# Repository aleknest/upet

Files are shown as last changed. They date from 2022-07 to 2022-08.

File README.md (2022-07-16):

# upet

[Відео роботи верстата](https://youtu.be/OY4By4eS6UQ)

[Список комплектуючих верстата](./bom/bom_machine.txt).

[Список комплектуючих підтримувача бобіни з лентою](./bom/bom_spool.txt).

[Список комплектуючих підтримувача бобіни з філаментом для принтера](./bom/bom_printer.txt).

Бобіни для порізаної ленти: https://www.thingiverse.com/thing:1848206

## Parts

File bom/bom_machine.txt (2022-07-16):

    100K NTC 3950 Thermistor
    4020 slot: 145mm
    685 bearing
    DIN 6798A washer
    Heater Cartridge 12V 40W 6*20mm
    Led power supply MN-100W12V, size 175*53*21mm, https://www.aliexpress.com/item/1005002290063769.html
    M3 nut (hex), 7 pcs
    M3 nut (thin square), 6 pcs
    M3 t-slot nut, 2 pcs
    M3 washer, 15 pcs
    M3x10 DIN912, 11 pcs
    M3x30 DIN912, 2 pcs
    M3x35 DIN912, 4 pcs
    M3x6 DIN912, 2 pcs
    M4 washer, 2 pcs
    M5 nut, 8 pcs
    M5 t-slot nut, 4 pcs
    M5 washer, 13 pcs
    M5x10 DIN912, 8 pcs
    M5x16 bolt, 2 pcs
    M5x16 DIN912
    M5x20 DIN912, 6 pcs
    M5x30 bolt
    M6x10 or M6x12 bolt
    Nema 17 motor
    optical switch
    Volcano heatblock

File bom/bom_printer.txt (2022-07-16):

    M5 nut, 8 pcs
    M5 t-slot nut, 2 pcs
    M5 washer, 8 pcs
    M5x10 DIN912, 2 pcs
    M5x16 bolt, 2 pcs
    M5x20 DIN912, 6 pcs

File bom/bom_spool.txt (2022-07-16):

    608 bearing
    M3 nut (hex), 2 pcs
    M3 washer, 2 pcs
    M3x20 DIN912, 2 pcs

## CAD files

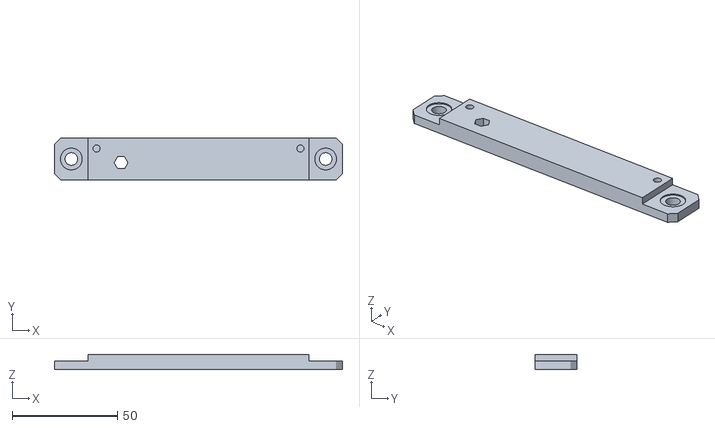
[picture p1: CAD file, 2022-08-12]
produce/board/plate.stl
137.0 x 20.0 x 6.99

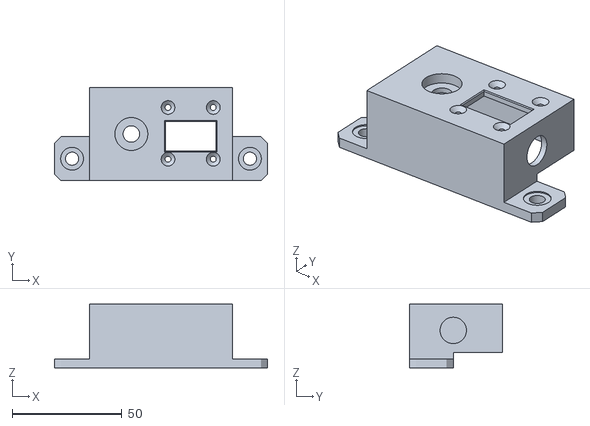
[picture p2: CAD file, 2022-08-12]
produce/display/box.stl
97.0 x 42.5 x 29.1

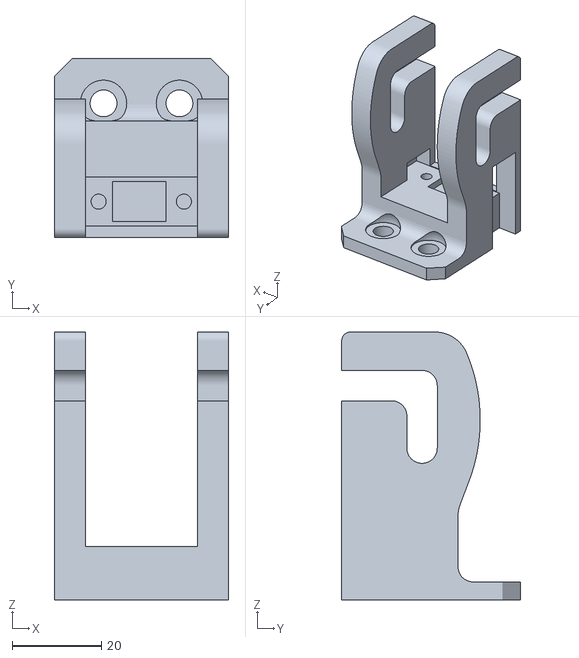
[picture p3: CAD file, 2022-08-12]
produce/main/endstop.stl
39.0 x 40.0 x 60.0

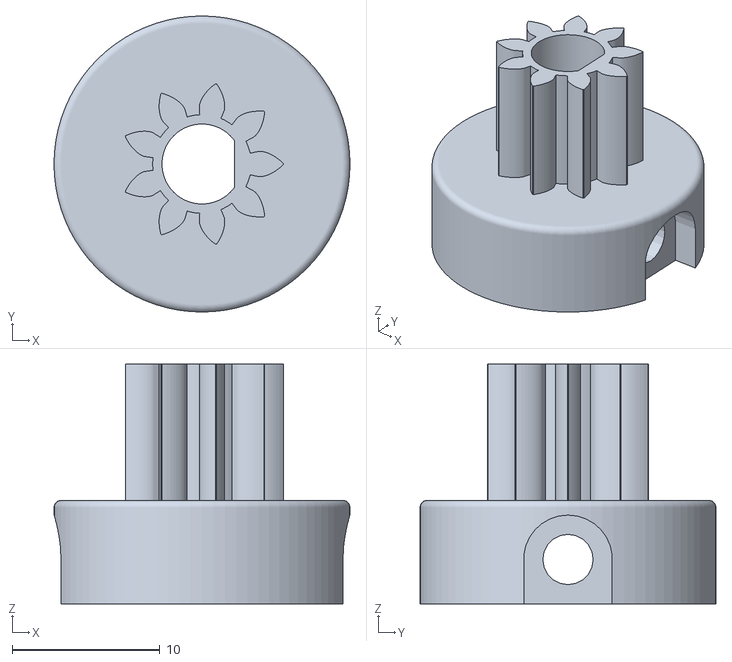
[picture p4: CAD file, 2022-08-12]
produce/planetary/planetary_sun.stl
20.0 x 20.0 x 16.2

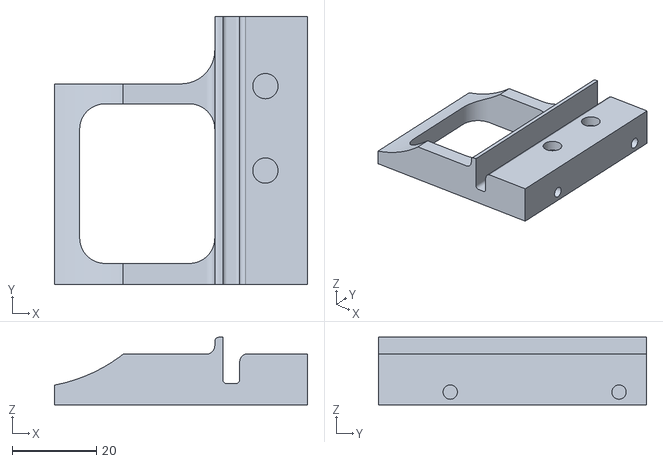
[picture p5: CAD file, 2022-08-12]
produce/power_supply/fix_left.stl
60.0 x 63.5 x 16.0

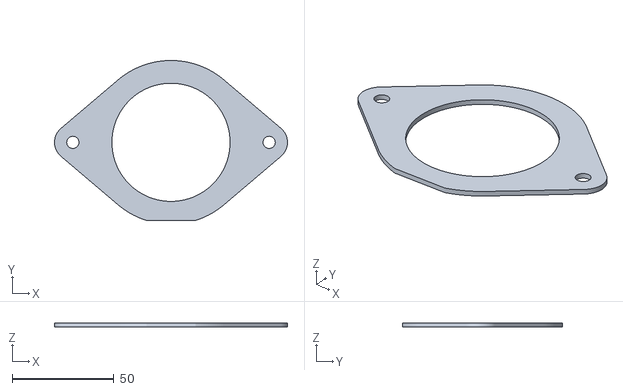
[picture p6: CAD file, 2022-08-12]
produce/printer/filament_case_top.stl
114.4 x 78.6 x 2.00

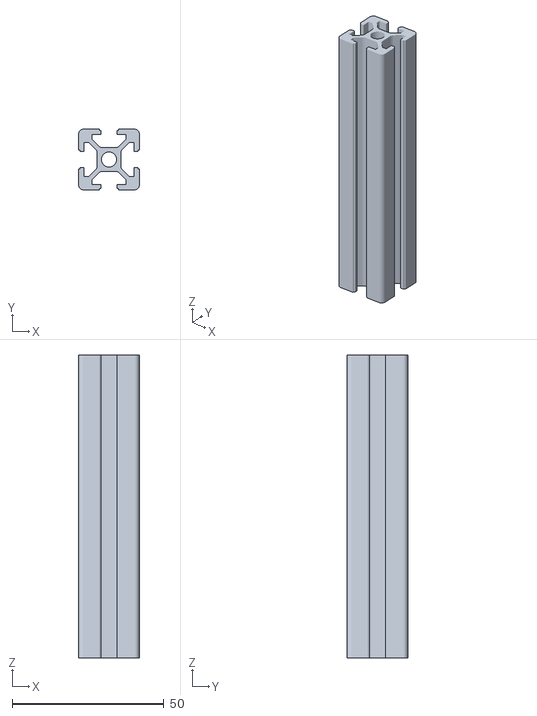
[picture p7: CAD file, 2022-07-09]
proto/slot2020.stl
20.0 x 20.0 x 100.0

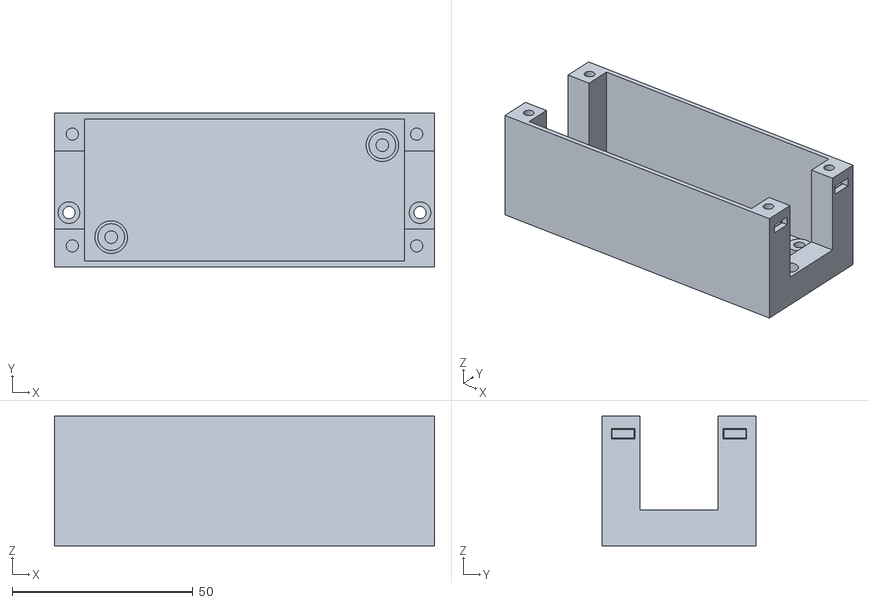
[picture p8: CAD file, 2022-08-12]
produce/board/bottom.stl
105.0 x 42.5 x 35.9

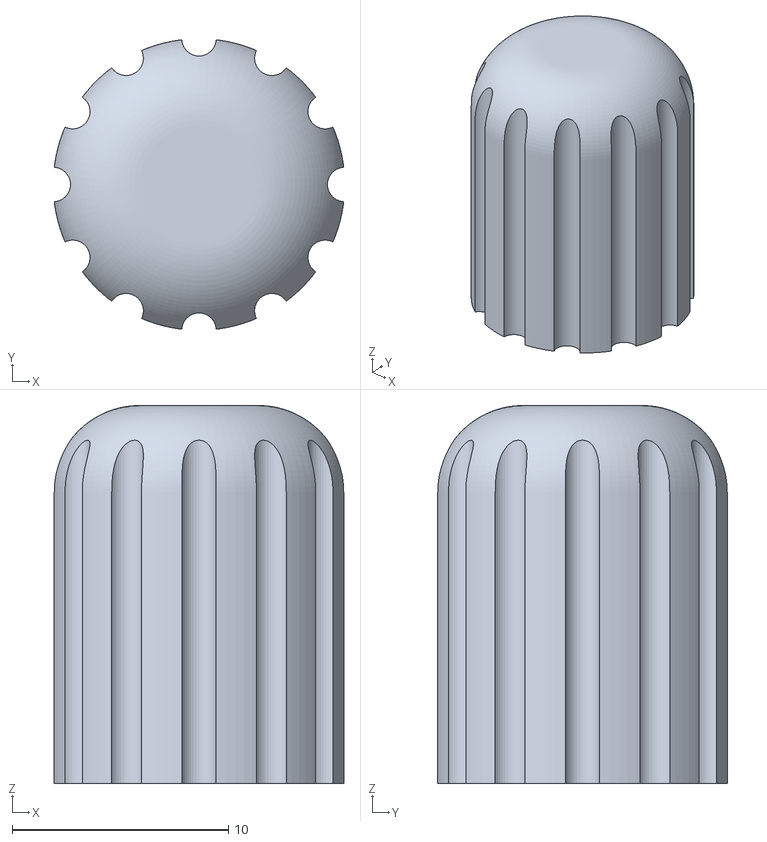
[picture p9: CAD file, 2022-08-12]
produce/display/encoder_knob.stl
13.4 x 13.4 x 17.5

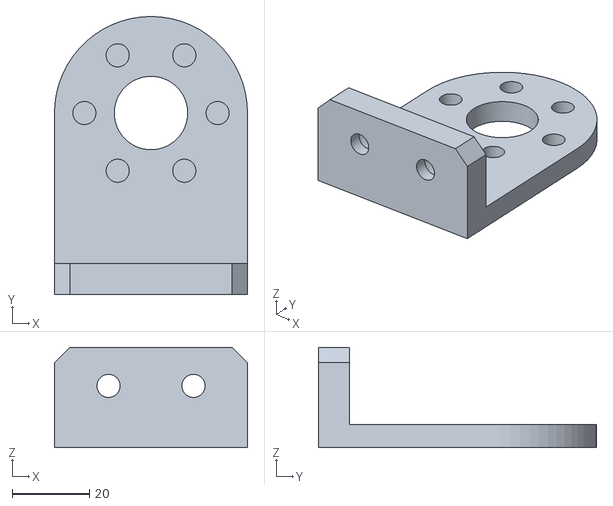
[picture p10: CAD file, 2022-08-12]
produce/main/stand.stl
50.0 x 72.0 x 26.0

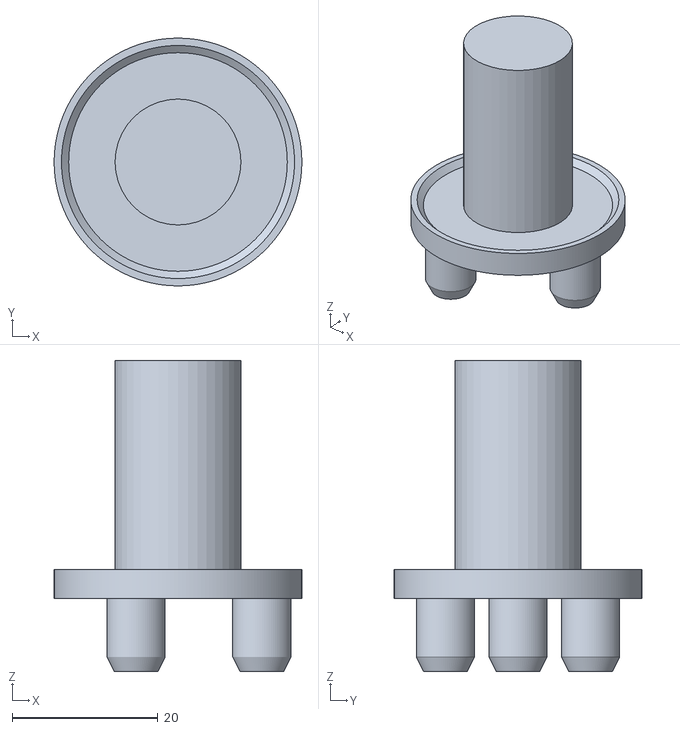
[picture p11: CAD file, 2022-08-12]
produce/planetary/planetary_carrier.stl
34.0 x 34.0 x 42.7

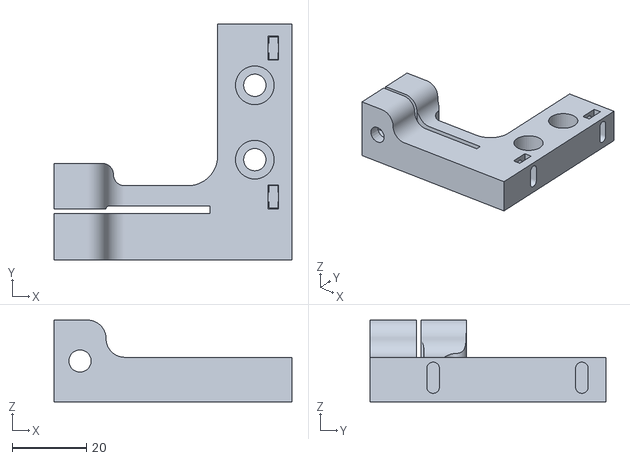
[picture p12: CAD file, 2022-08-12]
produce/power_supply/fix_right.stl
64.0 x 63.5 x 22.0

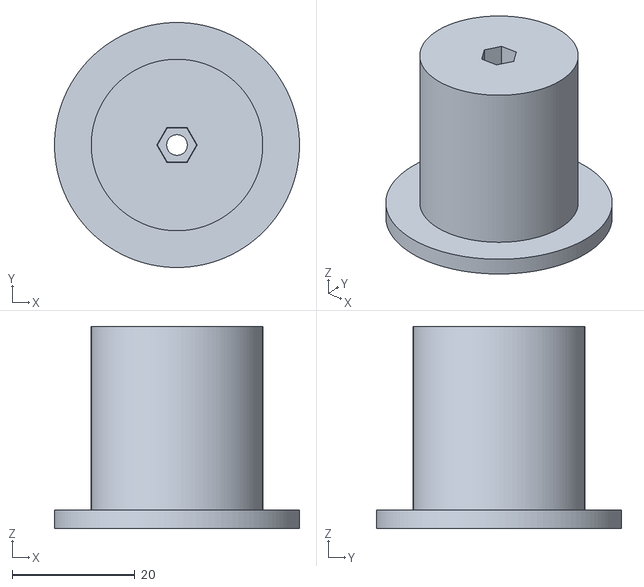
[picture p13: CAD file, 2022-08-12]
produce/spool/top.stl
40.0 x 40.0 x 33.0

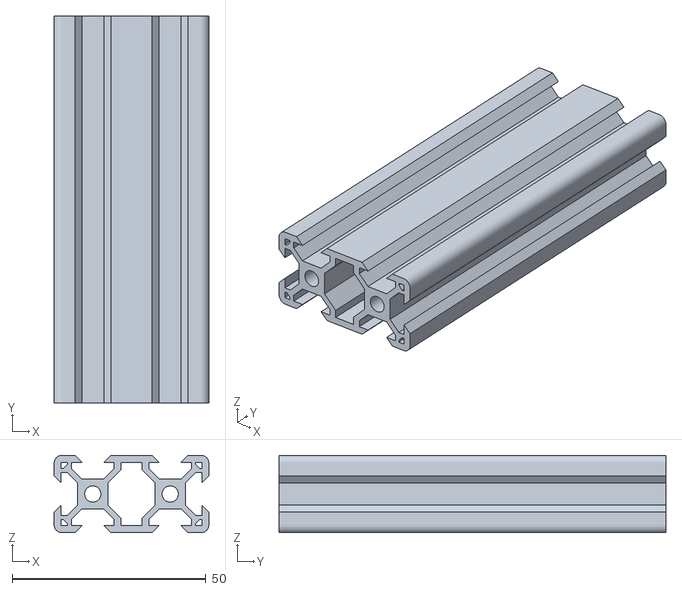
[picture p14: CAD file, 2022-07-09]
proto/40x20x100VSlotExtrusion.stl
40.0 x 100.0 x 20.0

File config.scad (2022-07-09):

include <../_utils_v2/NopSCADlib/core.scad>
include <../_utils_v2/NopSCADlib/vitamins/stepper_motors.scad>
include <../_utils_v2/NopSCADlib/vitamins/extrusion_brackets.scad>

use <../_utils_v2/Getriebe.scad>
use <../_utils_v2/_round/polyround.scad>
use <../_utils_v2/fillet.scad>
use <../_utils_v2/m3-m8.scad>

slot=40;

//                          corner  body    boss    boss          shaft
//                          side, length, radius, radius, radius, depth, shaft, length,      holes, cap heights
NEMA17ali  = ["NEMA17ali",   42.3, 38.3,     53.6/2, 25,     11,     2,     5,     24,          31,    [11.5,  9]];

eingriffswinkel=10;
gear_big_steigungswinkel=10;
gear_big_modul=1;
gear_big_d=70;
gear_small_d=3;
gear_big_h=8-2;
gear_small_h=30;
small_gear_r = gear_small_d/(2*sin(gear_big_steigungswinkel));

filament_fix_screw=18+2;	

// inner diameter, outer diameter, height, cap diameter,cap thickness
body_dim = [33-13,60-18,40,gear_big_d,3];
big_gear_tr=[[0,0,gear_big_d/2],[0,90,-90]];
big_gear_mirror=false;
small_gear_mirror=true;
small_gear_block_mirror=false;
small_gear_angle=180;//75+60;
small_gear_tr=[[0,0,-small_gear_r],[0,0,90]];
small_gear_fix_tr=[[gear_small_h/2+4,0,-small_gear_r],[0,0,90]];
motor_tr=[vec_add(small_gear_tr[0],[-40,0,0]),[0,90,0]];
small_gear_pad_tr=[vec_add(motor_tr[0],[4,0,0]),motor_tr[1]];

small_gear_pad=[small_gear_r*2,abs(motor_tr[0].z-small_gear_tr[0].z)
	+abs(motor_tr[0].x-small_gear_tr[0].x)-16.8];
// inner diameter, height, cap diameter,cap thickness
spool_axis=[body_dim[0]-1,body_dim[2],body_dim[0]+30,14];
spool_axis_tr=[[0,0,gear_big_d/2],[90,0,0]];

stand_zadd=4;
stand_slot_th=8;
//width,height,thickness,spool fix diameter and thickness
stand = [50,gear_big_d/2,6,spool_axis[2],6];
stand_tr=[[0,spool_axis[3],0],[90,0,180]];

// outer,height,inner
bearings = [
 [10,4,5] //mr105zz
,[11,5,5] //685zz
,[16,5,5] //625zz
,[10,4,3] //623zz
,[9,3,5] //mr95
,[16,5,8] //688zz
,[22,7,8] //608zz
];
small_gear_bearing=bearings[1];
//thickness,bottom
small_gear_bearing_p=3;
nobearing=false;

slot_length=145;
slot_tr=[slot_length/2-30,-slot+20,-stand_slot_th-stand_zadd-10];
volcano_tr=[slot_length-55,-12,-3.5];
brdiff=14.2;
bradd=1+0.3;
bracket_tr_y=volcano_tr.y+26;
bracket_tr_z=volcano_tr.z-8.5;
bracket_outer=[4,3];
bracket_tr=[
	  [[volcano_tr.x-brdiff+bradd,bracket_tr_y,bracket_tr_z],[0,0,-90]]
	 ,[[volcano_tr.x+brdiff+bradd,bracket_tr_y,bracket_tr_z],[0,0,-90]]
];


power_to_slot_out=7.5+3;
power_to_slot_left_dim=[24/2,53+power_to_slot_out,20+40];
power_to_slot_right_fix=14;
power_to_slot_right_x=10;
power_to_slot_right_dim=[24/2+power_to_slot_right_x,53+power_to_slot_out,50+power_to_slot_right_fix];
slot_left_tr=[[slot_tr.x-slot_length/2,slot_tr.y-power_to_slot_out/2+14,slot_tr.z-10],[0,0,0]];
slot_right_tr=[[slot_tr.x+slot_length/2,slot_tr.y-power_to_slot_out/2+14,slot_tr.z-10],[0,0,180]];
power_to_slot_up=[2,4];
power_to_slot_cut=[4,7];

endstop_thickness=3;
endstop_top=34+14+4;
endstop_dim=[31,26,4];
endstop_tr=[-12-60,-8-22-24,-4];

endstop_screw_d=6;
endstop_screw_out=2;
endstop_screw_tr=[10,22];

endstop_tube=14;

endstop_up=8;
endstop_back=40-20;

motor_out=2;

//thickness bottom
filament_case=[2,2+1.6+1.6];

spool_bearing=bearings[6];
// bottom part(bottom,top),bottom height; top part height,thickness,diameter
//,fix height diameter
spool_dim=[90,40,10+5,2,3,40,30,28];

oled_width=27.3;
oled_height=27.75;
screen_width=23;
screen_height=13.5;
function stand_tr(x,y)=[(oled_width/2-2.1-2.5/2)*x,(oled_height/2-2.1)*y-0.3,0];

function vec_add (v1,v2)=[v1.x+v2.x,v1.y+v2.y,v1.z+v2.z];
module translate_rotate(tr) 
{
	for (i=[0:$children-1]) 
		translate (tr[0])
		rotate(tr[1])
			children(i);
}

module rotate_small_gear()
{
	for (i=[0:$children-1]) 
		translate([0,0,gear_big_d/2])
		rotate([0,small_gear_angle,0])
		translate([0,0,-gear_big_d/2])
		mirror([small_gear_block_mirror?1:0,0,0])
			children(i);
}

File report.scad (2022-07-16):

is_reported=true;

module deb (s)
{
	if (is_reported)
	{
		//echo (str("<b style='color:green'>",s));
		echo (s);
	}
}

module report(s)
{
	deb(s);
}

module report_slot(h)
{
	deb(str("4020 slot: ",h,"mm"));
}

module report_m3_hexnut()
{
	deb(str("M3 nut (hex)"));
}

module report_m3_squarenut()
{
	deb(str("M3 nut (thin square)"));
}

module report_m3(screw)
{
	deb(str("M3x",screw," DIN912"));
}

module report_m3_washer()
{
	deb(str("M3 washer"));
}

module report_m4_washer()
{
	deb(str("M4 washer"));
}

module report_nema17()
{
	deb(str("Nema 17 motor"));
}

module report_optical_switch()
{
	deb(str("optical switch"));
}

module report_m5_screw_only(screw)
{
	deb(str("M5x",screw," DIN912"));
}

module report_m5_screw(screw)
{
	report_m5_screw_only(screw=screw);
	report_m5_washer();
}

module report_m5_nut()
{
	deb(str("M5 nut"));
}

module report_m5_washer()
{
	deb(str("M5 washer"));
}

module report_m5_bolt(screw)
{
	deb(str("M5x",screw," bolt"));
}

module report_m5_point()
{
	report_m5_screw(10);
	deb(str("M5 t-slot nut"));
}

module report_m3_slot_nut()
{
	deb(str("M3 t-slot nut"));
}

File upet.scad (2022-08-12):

cmd="";

include <../_utils_v2/NopSCADlib/core.scad>
include <../_utils_v2/NopSCADlib/vitamins/stepper_motors.scad>
include <../_utils_v2/NopSCADlib/vitamins/extrusion_brackets.scad>

use <../_utils_v2/Getriebe.scad>
use <../_utils_v2/_round/polyround.scad>
use <../_utils_v2/fillet.scad>
use <../_utils_v2/m3-m8.scad>

include <config.scad>
include <report.scad>
use <upet_planetary.scad>

gear_big_cut_offsd=2;

module cylinder_bevel(d,bevel,fn)
{
	rotate_extrude($fn=fn[1])
	translate ([d/2,0,0])
	difference()
	{
		square(size=bevel,center=false);
		translate ([bevel,bevel,0])
			circle (r=bevel,$fn=fn[0]);
	}
}

module proto_slot2020_cr(length)
{
	color ("#668866")
	translate ([0,0,0])
	scale ([1,1,length/100])
	translate ([0,0,-50])
		import ("proto/slot2020.stl");
}

module proto_slot4020_cr(length)
{
	color ("#668866")
	scale ([1,1,length/100])
	translate ([0,0,-50])
	rotate ([90,0,90])
		import ("proto/40x20x100VSlotExtrusion.stl");
	report_slot(h=length);
}

module proto_pet_volcano()
{
	translate ([31,44,3.12])
	rotate ([180,90,90])
		import ("proto/pet_volcano.stl");
	
	report ("Volcano heatblock");
	report ("Heater Cartridge 12V 40W 6*20mm");
	report ("100K NTC 3950 Thermistor");
	report ("M6x10 or M6x12 bolt");

	report_m3(screw=30);
	report_m3(screw=30);
	report_m3_slot_nut();
	report_m3_slot_nut();
	report_m3_washer();
	report_m3_washer();
	report_m4_washer();
	report_m4_washer();
	report_m5_washer();
	report_m5_washer();
}

module proto_slot()
{
	translate (slot_tr)
	translate (stand_tr[0])
	rotate ([0,90,0])
		proto_slot4020_cr(length=slot_length);
}

module proto()
{
	translate (volcano_tr)
		proto_pet_volcano();
	
	translate ([0,-motor_out,0])
	rotate_small_gear()
	translate_rotate (motor_tr)
		NEMA(NEMA17ali, shaft_angle = 0, jst_connector = false);
	report_nema17();
		
	proto_slot();
}

module gear_small()
{
	rotate_small_gear()
	translate ([0,-motor_out,0])
	difference()
	{
		union()
		{
			translate_rotate(small_gear_tr)
			translate ([-small_gear_r,0,0])
				translate ([0,small_gear_mirror?-4.4:0,0])
				mirror ([0,small_gear_mirror?1:0,0])
				schneckenradsatz_small(
					  modul=gear_big_modul
					, zahnzahl=gear_big_d
					, gangzahl=gear_small_d
					, breite=gear_big_h
					, laenge=gear_small_h
					, bohrung_schnecke=0
					, bohrung_rad=0
					, eingriffswinkel=eingriffswinkel
					, steigungswinkel=gear_big_steigungswinkel
					, optimiert=false
					, zusammen_gebaut=true
				);
			translate_rotate (small_gear_pad_tr)
				cylinder(d=small_gear_pad[0],h=small_gear_pad[1],$fn=40);
				
			translate_rotate (small_gear_pad_tr)
			{
				dd=nobearing?small_gear_bearing[0]:small_gear_bearing[2]-0.4;
				hadd=nobearing?dd/2:0;
				hh=(24+gear_small_h+small_gear_bearing[1]+1)-dd/2;
				cylinder(d=dd,h=hh+hadd,$fn=80);
				translate ([0,0,hh])
					sphere (d=dd,$fn=80);
			}
		}
		
		translate_rotate (small_gear_pad_tr)
		translate ([0,0,-0.01])
			cylinder(d=5+0.4,h=24+gear_small_h-6,$fn=40);
			
		translate_rotate (small_gear_pad_tr)
		rotate ([90,0,0])
		translate ([0,12,-7])
		{
			screw=6;
			m3_screw(h=screw,cap_out=10);
			translate ([0,0,screw-4.8])
			rotate ([0,0,180])
				m3_square_nut();
		}
	}
}
      
module cylinder_bevel_outer(d,bevel,fn)
{
	rotate_extrude($fn=fn[1])
	{
		square(size=[d/2-bevel,bevel],center=false);
		translate ([d/2-bevel,bevel,0])
		difference()
		{
			circle (r=bevel,$fn=fn[0]);
			translate ([-bevel,0,0])
				square(size=[bevel*2,bevel],center=false);
		}
	}
}

gear_cut=[gear_big_d-10,gear_big_h-4];
fil_rays=10;

module gear_big_fix(add=false,part="",report=false)
{
	screw=10;
	rays=3;
	angle=360/rays;
	
	topcut=part=="top"?4:0;
	
	cut_shape_h=body_dim[2]-body_dim[4];
	cut=[2.4,2.4,10];
	hh=14;
	cut_shape_r=2;
	cut_shape2_up=11;
	module cut_shape(offs=[0,0])
	{
		offset(r=cut_shape_r)
		offset(delta=-cut_shape_r)
		difference()
		{
			circle(d=body_dim[1]-cut[0]*2+offs[0]*2,$fn=100);
			circle(d=body_dim[0]+cut[1]*2-offs[1]*2,$fn=100);
			for (a=[0:rays-1])
				rotate ([0,0,-angle/2+a*angle+angle/2])
				translate ([-cut[2]/2,0])
					square ([cut[2],body_dim[1]]);
		}
	}
	module cut_shape2(offs=[0,0])
	{
		offset(r=cut_shape_r)
		offset(delta=-cut_shape_r)
		difference()
		{
			circle(d=body_dim[1]-cut[0]*2+offs[0]*2,$fn=100);
			circle(d=body_dim[0]+cut[1]*2-offs[1]*2,$fn=100);
		}
	}
	module lock_cut()
	{
		translate ([0,0,body_dim[2]-body_dim[4]-hh-topcut])
		rotate ([0,0,-angle/2-90])
		rotate_extrude(angle=angle,$fn=60)
			square ([body_dim[0],hh+topcut*2]);
	}
	
	if ((part=="middle")&& add)
	{
		intersection()
		{
			translate ([0,0,cut_shape_h-hh])
			linear_extrude (0.2)
				cut_shape(offs=cut);
			lock_cut();
		}
	}
	if ((part=="middle" || part=="top")&&(!add))
	{
		difference()
		{
			union()
			{
				linear_extrude (cut_shape_h+topcut)
					cut_shape();		
				translate ([0,0,cut_shape2_up])
				linear_extrude (cut_shape_h+topcut-cut_shape2_up*2)
					cut_shape2();		
			}
			lock_cut();
		}
	}
	if ((part=="bottom")&&(!add))
	{
		translate ([0,0,-gear_big_h/2-0.01])
		difference()
		{
			linear_extrude (cut_shape_h+topcut)
				cut_shape();
			
			lock_cut();
		}
	}
	
	for (a=[0:rays-1])
	{
		rr=4;
		rotate ([0,0,-angle/2+a*angle+angle/2])
		translate ([0,(body_dim[0]+body_dim[1])/4,0])
		{
			nutdiff=3;
			if (add)
			{
				protect=0.3;
				
				translate ([0,0,m3_nut_h()+0.2])
				translate ([0,0,screw-nutdiff])
				rotate([0,0,90])
					m3_nut(h=0.3);
				
				translate ([0,0,body_dim[2]])
				rotate ([180,0,180])
				translate ([0,0,-0.2])
				translate ([0,0,screw-nutdiff])
				rotate([0,0,90])
					m3_nut(h=protect);			
			}
			else
			{
				for (p=[
					[[0,0,0],[0,0,0]]
					,[[0,0,body_dim[2]],[180,0,180]]
					])
				translate (p[0])
				rotate (p[1])
				{
					if (report)
					{
						report_m3_hexnut();
						report_m3(screw=screw);
						report_m3_washer();
					}
					
					m3_screw(h=screw+2);
					m3_washer();
					
					translate ([0,0,screw-nutdiff])
					rotate([0,0,90])
					hull()
					{
						nut(G=m3_nut_G()+0.2,H=m3_nut_h()+0.2);
						translate ([20,0,0])
							nut(G=m3_nut_G()+0.2,H=m3_nut_h()+0.2);
					}
				}
			}
		}
	}
}

module gear_big(part="",report=false)
{
	rr=body_dim[1]/2-(body_dim[1]-body_dim[0])/4;
	washer_fix_hh=4;
	
	translate_rotate(big_gear_tr)
	union()
	{
		difference()
		{
			union()
			{
				if (part!="middle" && part!="top")
				translate ([gear_big_d/2,0,0])
				mirror([0,big_gear_mirror?1:0,0])
				{
					schneckenradsatz_big(
						modul=gear_big_modul
						, zahnzahl=gear_big_d
						, gangzahl=gear_small_d
						, breite=gear_big_h
						, laenge=gear_small_h
						, bohrung_schnecke=0
						, bohrung_rad=0
						, eingriffswinkel=eingriffswinkel
						, steigungswinkel=gear_big_steigungswinkel
						, optimiert=false
						, zusammen_gebaut=true
					);
				}
				
				cylinder (d=body_dim[1],h=body_dim[2]-body_dim[4]+0.01,$fn=100);
				
				//translate ([0,0,body_dim[2]-body_dim[4]])
					//cylinder (d=body_dim[3],h=body_dim[4],$fn=200);
				
				union()
				{
					hh=body_dim[4];
					dhh=body_dim[4]-hh;
					
					translate ([0,0,body_dim[2]-body_dim[4]])
						cylinder (d=body_dim[3],h=hh,$fn=200);
				
					translate ([0,0,body_dim[2]-body_dim[4]])
					{
						fn=200;
						cylinder (d=body_dim[1],h=hh+0.01,$fn=fn);
						translate ([0,0,hh])
							cylinder(d1=body_dim[1]+dhh*2,d2=body_dim[1],h=dhh,$fn=fn);
					}
				
					translate ([0,-rr,body_dim[2]-body_dim[4]])
					{
						fn=100;
						dd=m5_screw_diameter()+8;
						cylinder(d=dd+dhh*2,h=hh+0.01,$fn=fn);
						translate ([0,0,hh])
							cylinder(d1=dd+dhh*2,d2=dd,h=dhh,$fn=fn);
					}
				}
				
				
			}
			
			translate ([0,0,body_dim[2]+0.1])
			{
				angle=360/fil_rays;
				dd=4;
				for (a=[0:fil_rays-1]) let (ar=a*angle)
					rotate ([180,0,ar])
					translate ([body_dim[3]/2-dd/2-3,0,0])
						cylinder (d=dd,h=body_dim[4]+0.2,$fn=20);
			}
			
			translate ([0,0,-20])
				cylinder (d=body_dim[0],h=100,$fn=60);
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

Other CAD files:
produce/board/top.stl
produce/main/gear_big_middle.stl
produce/planetary/planetary_carrier_bottom.stl
produce/spool/top_inner.stl
upet_planetary.scad
produce/main/endstop_flag.stl
produce/main/gear_big_top.stl
produce/main/motor_plate.stl
produce/main/screw_cap.stl
produce/main/spool_axis.stl
produce/planetary/planetary_body.stl
produce/planetary/planetary_satellite.stl
produce/planetary/planetary_top.stl
produce/spool/washer.stl
proto/corner2020.stl

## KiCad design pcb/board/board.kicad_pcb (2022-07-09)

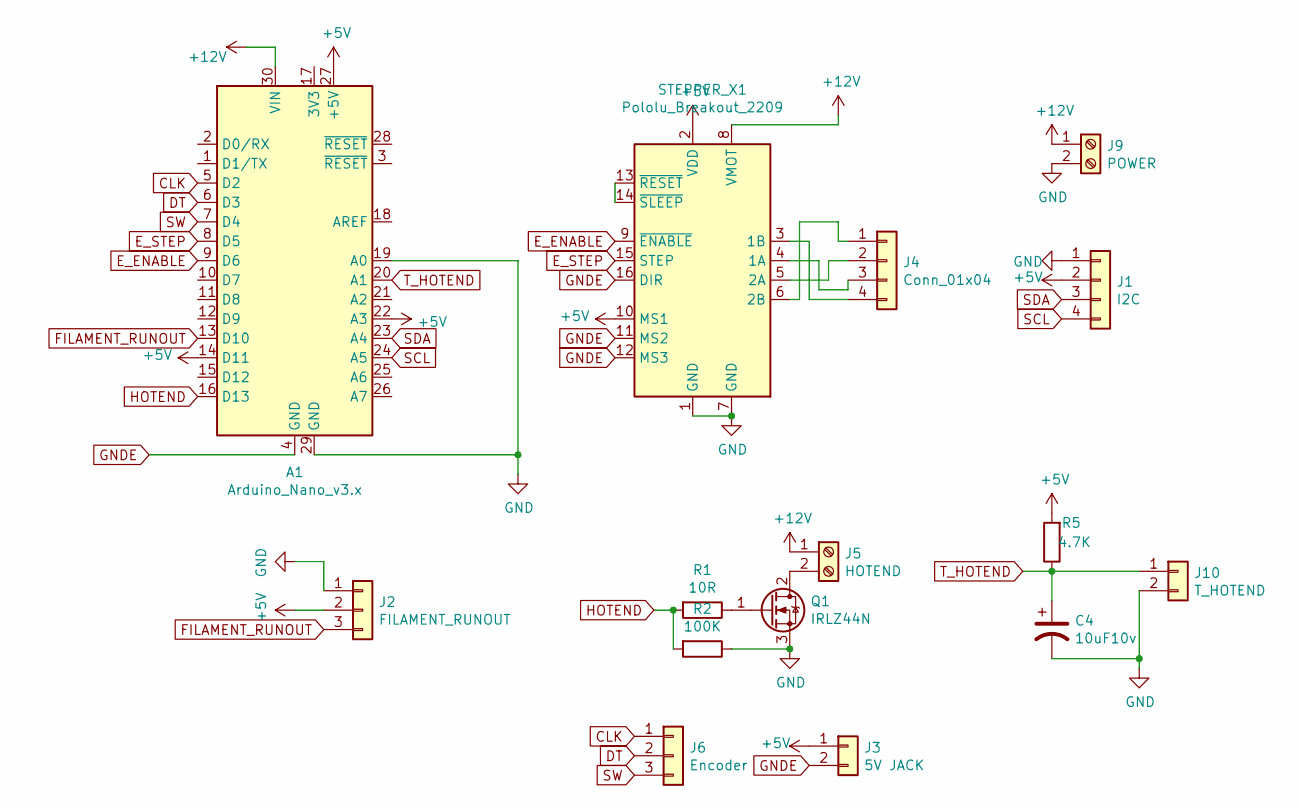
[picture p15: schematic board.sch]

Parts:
A1: Arduino_Nano_v3.x; Arduino_Nano
C4: 10uF10v; CP_EIA-3216-12_Kemet-S_Pad1.58x1.35mm_HandSolder
J1: I2C; PinHeader_1x04_P2.54mm_Vertical
J2: FILAMENT_RUNOUT; PinHeader_1x03_P2.54mm_Vertical
J3: 5V JACK; PinHeader_1x02_P2.54mm_Vertical
J4: Conn_01x04; PinHeader_1x04_P2.54mm_Vertical
J5: HOTEND; TerminalBlock_Phoenix_MKDS-1,5-2_1x02_P5.00mm_Horizontal
J6: Encoder; PinHeader_1x03_P2.54mm_Vertical
J9: POWER; TerminalBlock_Phoenix_MKDS-1,5-2_1x02_P5.00mm_Horizontal
J10: T_HOTEND; PinHeader_1x02_P2.54mm_Vertical
Q1: IRLZ44N; TO-220-3_Vertical
R1: 10R; R_Axial_DIN0207_L6.3mm_D2.5mm_P7.62mm_Horizontal
R2: 100K; R_Axial_DIN0207_L6.3mm_D2.5mm_P7.62mm_Horizontal
R5: 4.7K; R_Axial_DIN0207_L6.3mm_D2.5mm_P7.62mm_Horizontal
STEPPER_X1: Pololu_Breakout_2209; Pololu_Breakout-16_15.2x20.3mm

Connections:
+5V: A1.14 (D11), A1.22 (A3), A1.27 (+5V), J1.2, J2.2, J3.1, R5.2, STEPPER_X1.2 (VDD), STEPPER_X1.10 (MS1)
+12V: A1.30 (VIN), J5.1, J9.1, STEPPER_X1.8 (VMOT)
CLK: A1.5 (D2), J6.1
DT: A1.6 (D3), J6.2
E_ENABLE: A1.9 (D6), STEPPER_X1.9 (~ENABLE)
E_STEP: A1.8 (D5), STEPPER_X1.15 (STEP)
FILAMENT_RUNOUT: A1.13 (D10), J2.3
GND: A1.19 (A0), A1.29 (GND), C4.2, J1.1, J2.1, J9.2, J10.2, Q1.3 (S), R2.1, STEPPER_X1.1 (GND), STEPPER_X1.7 (GND)
GNDE: A1.4 (GND), J3.2, STEPPER_X1.11 (MS2), STEPPER_X1.12 (MS3), STEPPER_X1.16 (DIR)
HOTEND: A1.16 (D13), R1.2, R2.2
unnamed: J4.1, STEPPER_X1.6 (2B)
unnamed: J4.2, STEPPER_X1.5 (2A)
unnamed: J4.3, STEPPER_X1.4 (1A)
unnamed: J4.4, STEPPER_X1.3 (1B)
unnamed: J5.2, Q1.2 (D)
unnamed: Q1.1 (G), R1.1
unnamed: STEPPER_X1.13 (~RESET), STEPPER_X1.14 (~SLEEP)
SCL: A1.24 (A5), J1.4
SDA: A1.23 (A4), J1.3
SW: A1.7 (D4), J6.3
T_HOTEND: A1.20 (A1), C4.1, J10.1, R5.1

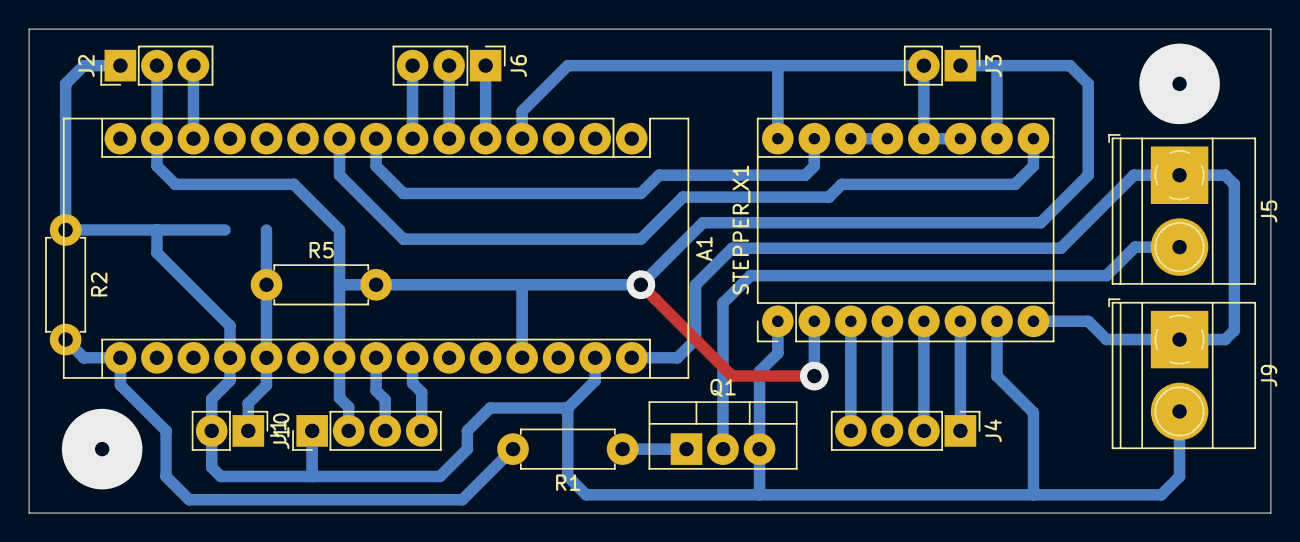
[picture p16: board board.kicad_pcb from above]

Board: 2 copper layers, 86.4 x 33.7 mm, 15 parts (1 on the bottom side), 21 nets.

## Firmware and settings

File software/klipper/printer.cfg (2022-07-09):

[include kiauh_macros.cfg]
[pause_resume]
#[display_status]
[virtual_sdcard]
path: ~/gcode_files

[board_pins arduino-standard]
aliases:
    ar0=PD0, ar1=PD1, ar2=PD2, ar3=PD3, ar4=PD4,
    ar5=PD5, ar6=PD6, ar7=PD7, ar8=PB0, ar9=PB1,
    ar10=PB2, ar11=PB3, ar12=PB4, ar13=PB5, ar14=PC0,
    ar15=PC1, ar16=PC2, ar17=PC3, ar18=PC4, ar19=PC5,
    analog0=PC0, analog1=PC1, analog2=PC2, analog3=PC3, analog4=PC4,
    analog5=PC5, analog6=PE2, analog7=PE3 

[mcu]
serial: /dev/serial/by-id/usb-1a86_USB_Serial-if00-port0
baud: 57600

[printer]
kinematics: none
max_velocity: 1000
max_accel: 4000

[display]
lcd_type:ssd1306
click_pin: ar3
encoder_pins: ar2,ar4


[extruder]
sensor_type: ATC Semitec 104GT-2
sensor_pin: analog2
pullup_resistor: 4700
microsteps: 16
rotation_distance: 268
nozzle_diameter: 0.400
filament_diameter: 1.75
step_pin: ar5
dir_pin: ar8
enable_pin: !ar6
heater_pin: ar12
control = pid
pid_kp = 19.371
pid_ki = 0.755
pid_kd = 124.218
min_extrude_temp: 0
min_temp: 0
max_temp: 300
max_extrude_only_distance: 10000000.0
max_extrude_cross_section: 4000.0

[verify_heater extruder]
max_error: 240
check_gain_time:20
heating_gain: 1
hysteresis: 10

[filament_switch_sensor f_sensor]
pause_on_runout: False
runout_gcode:
    FIRMWARE_RESTART
#    M112
switch_pin: ar10

[respond]

[delayed_gcode SFEED]
initial_duration: 0.0
gcode:
  G91
  G1 E100 F{printer['gcode_macro DFEED'].speed}
  G90
  UPDATE_DELAYED_GCODE ID=SFEED DURATION=0.0001

[gcode_macro DFEED]
variable_speed: 0
gcode:
  {% if 'S' in params %}
  {% set S = params.S|int %}
    SET_FILAMENT_SENSOR SENSOR=f_sensor ENABLE=1
    M118 FEED {S}
    SET_GCODE_VARIABLE MACRO=DFEED VARIABLE=speed VALUE={S}
    UPDATE_DELAYED_GCODE ID=SFEED DURATION=0.01
  {% endif %}

[gcode_macro STOP]
gcode: 
  UPDATE_DELAYED_GCODE ID=SFEED DURATION=0
  TURN_OFF_HEATERS
  M18
 
[gcode_macro F1200]
gcode: DFEED S=1200
[gcode_macro F1600]
gcode: DFEED S=1600
[gcode_macro F2000]
gcode: DFEED S=2000
[gcode_macro F2400]
gcode: DFEED S=2400
[gcode_macro F2800]
gcode: DFEED S=2800
[gcode_macro F3200]
gcode: DFEED S=3200
[gcode_macro F3800]
gcode: DFEED S=3800
[gcode_macro F4200]
gcode: DFEED S=4200

[gcode_macro PET_HEAT_ON]
gcode:
  SET_HEATER_TEMPERATURE HEATER=extruder TARGET=220
